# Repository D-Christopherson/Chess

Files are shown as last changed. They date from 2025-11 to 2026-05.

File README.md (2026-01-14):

This repo contains all the relevant files for a chess board I'm building.

The top level directory contains a chess engine I wrote in Kotlin, serve with Spring Boot, and deploy to AWS with Terraform.
I'd written a chess engine in Java using two-dimensional arrays to represent the board early on in college, so I wanted 
to try bitboards this time. The goal is to represent the board as a set of 64-bit numbers since operations with those should 
be much faster than an array. 

Some hand wavy math for moving a rook up one square:
* One clock cycle to multiply the first index by the width of the outer array
* One clock cycle to add that to the base address of the array
* One clock cycle to multiply the second index by the data type the inner array contains
* One clock cycle to add that to the address calculated in step 2
* One clock cycle to null out that square
* Repeat above for the target square

With bitboards (ideally)
* One clock cycle to left shift the number representing the rook by 8

`chess_electronics` contains the schematic and PCB design for the circuit board that connects the microcontroller, RFID 
reader, and antennas together. These were created in KiCad.

`microcontroller` contains the code running on the ESP32. The microcontroller is responsible for controlling the 8 separate
8 way switches, driving the RFID reader over UART, and converting the RFID tags into pieces to create the actual game state.

`mobile_app` contains a proof of concept android app that reads the board state from the microcontroller over bluetooth 
and sends that state to the chess engine in AWS over the internet. The ESP32 could do this itself since it has Wi-Fi capabilities,
but it'd be a huge pain to reprogram the Wi-Fi credentials if I want to take the board to a club.

Here's an MS Paint breakdown of the board itself.

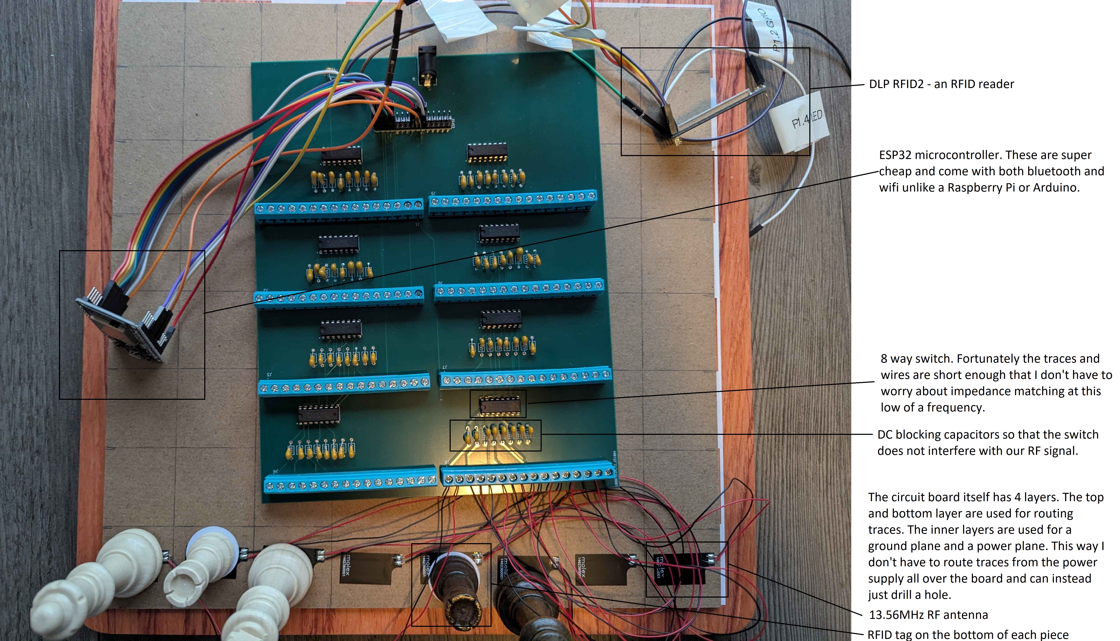
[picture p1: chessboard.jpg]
Chessboard


Eventually I'd like to strap an electromagnet to a pair of linear slides under the board to have the board play against 
a human. This product already exists, but costs between \$500 and \$1100.
The bill of materials for this build so far is:
* ESP32 dev board - $16 for a 3 pack on Amazon
* 8x SN74LV4051AN 8 way switch - $5.52 for 10 on DigiKey (cheaper than buying 8)
* 64x 13.56MHz RF antennas - $32 on DigiKey
* 65x 10nF ceramic capacitor - I bought a variety pack and used 47 nF capacitors after running out of 10nF. These will cost 
\$5-$30 on DigiKey. They just need to be capacitors that don't have polarity and are large enough to not add a ton of impedance 
(10nF is plenty).
* 8x 16 position screw terminals - $16 on DigiKey. I bought these not realizing that they're just 2 and 3 position terminals
connected to each other with a little plastic slide. Buying 64x 2 position terminals might be cheaper.
* DLP RFID2 - $37.95 on DigiKey. I've read that this chip is pretty outdated and has some firmware bugs. There might be 
something cheaper nowadays. The key is just to make sure it's compatible with the same frequency as the tags/antennas used 
and also has a pin for an external antenna.
* 5x circuit boards (as that's the minimum quantity most factories will make) - ~\$120. I also have a directory in `chess_electronics` 
called `Modular_Antenna` which crams the screw terminals and capacitors into a small board independent of one that would 
house the microcontroller and RFID reader (I have not designed this motherboard yet). This should bring the cost down to 
$30 or so since there's less wasted space. I'm just not sure if it's acceptable to run signal lines so close to other traces.

For the LCD screen you'll also need:
* 1x LCD screen - I'm using an LCD1602 module. It looks like these run \$5-\$10 depending on the source.
* 8x normally closed (Form B) relays. I quickly ran out of GPIO pins wiring each INH pin of the multiplexers to the
microcontroller directly, so these are going to connect the power plane to the INH pin. I'll have a 9th multiplexer that
connects to each of the relays. This brings the pins used for the multiplexers down to 6 from 11.
* 2x additional multiplexers. One for the multiplexer that now controls the INH pins and one for the LCD screen module.
The LCD screen has 8 data pins which the multiplexer will control as well as three pins for controlling the data on screen
and one pin for contrast.

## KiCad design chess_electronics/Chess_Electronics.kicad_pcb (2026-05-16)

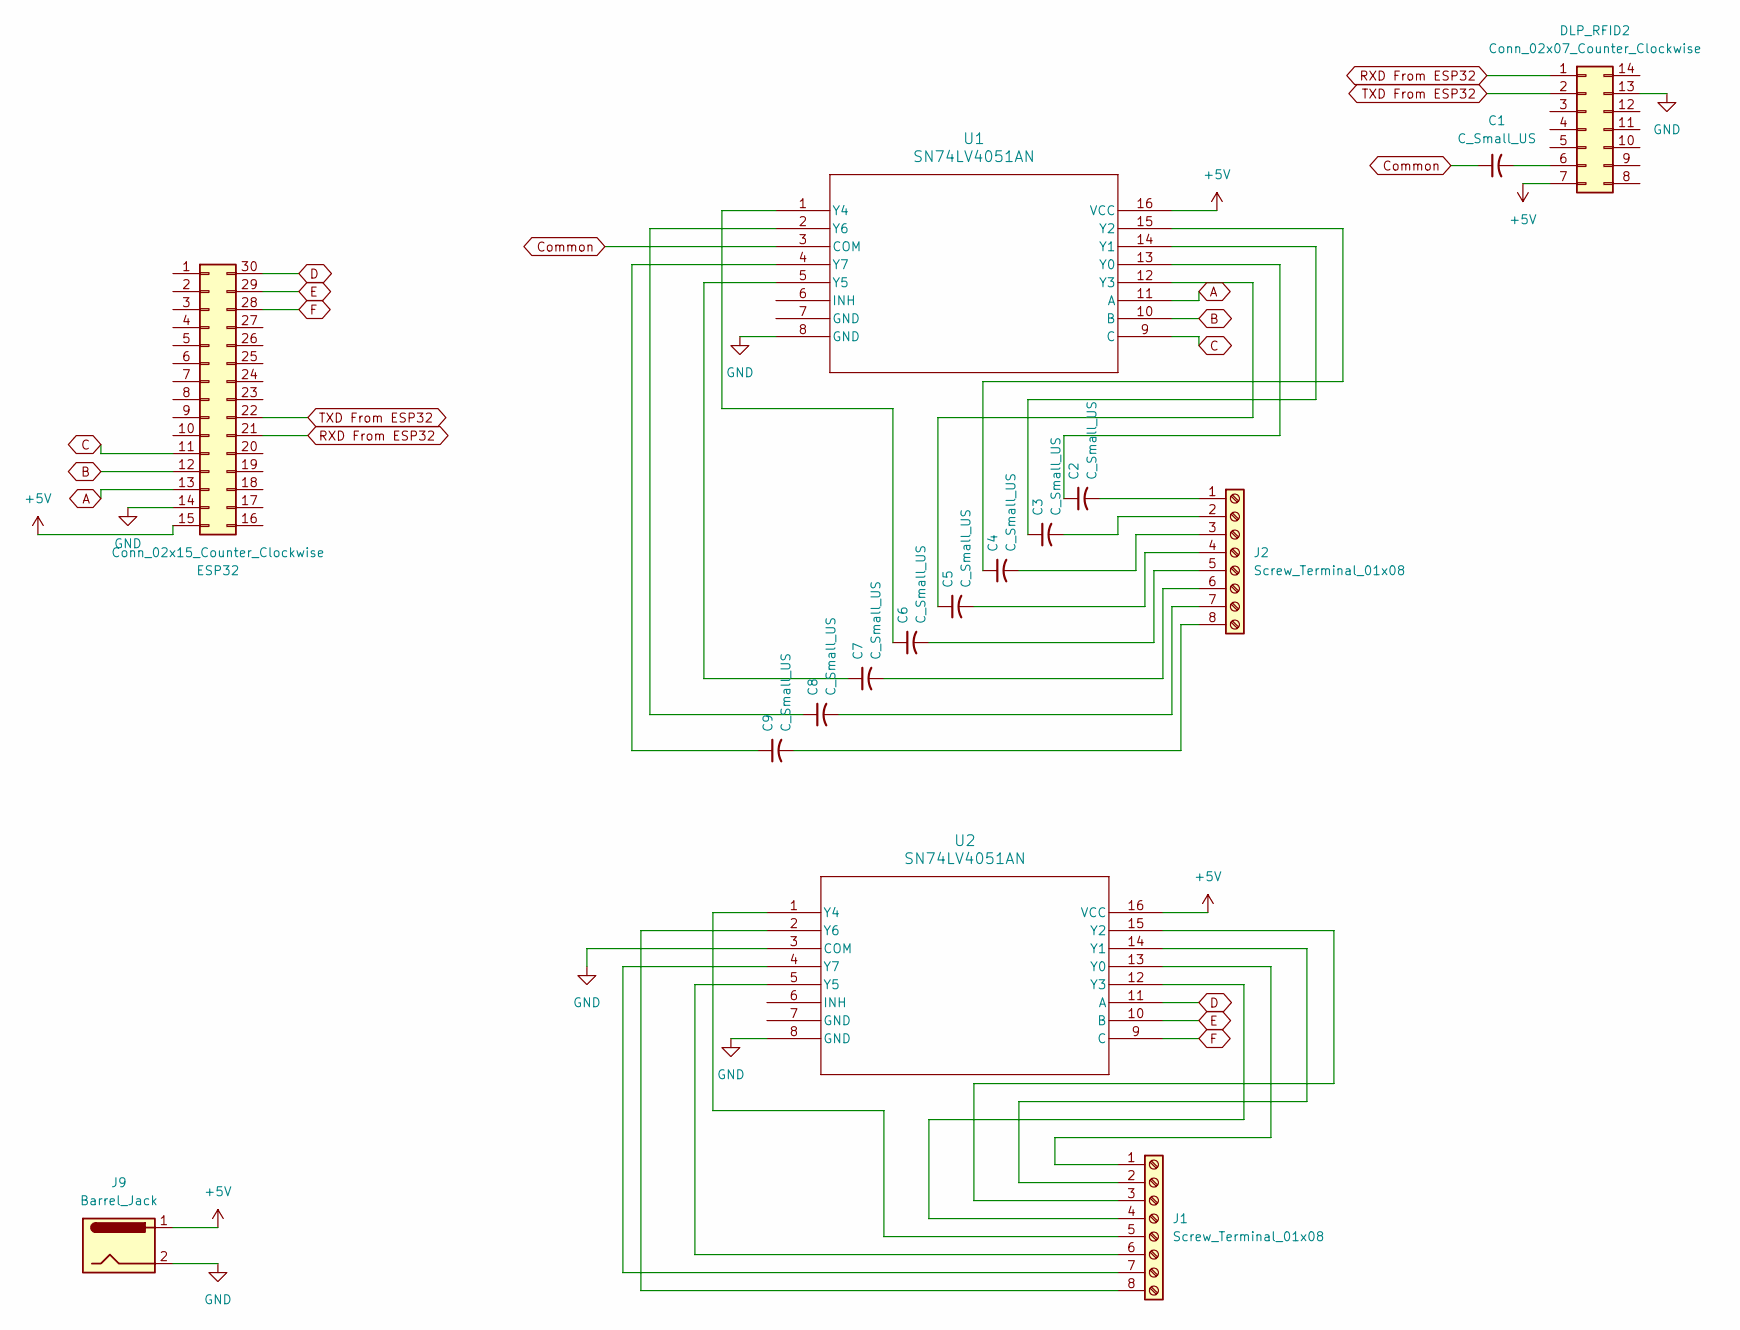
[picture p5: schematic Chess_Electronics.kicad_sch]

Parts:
C1, C2, C3, C4, C5, C6, C7, C8, C9: C_Small_US; C_Axial_L3.8mm_D2.6mm_P7.50mm_Horizontal
DLP_RFID2: Conn_02x07_Counter_Clockwise; PinHeader_2x07_P2.54mm_Vertical
ESP32: Conn_02x15_Counter_Clockwise; PinHeader_2x15_P2.54mm_Vertical
J1, J2: Screw_Terminal_01x08; TerminalBlock_MaiXu_MX126-5.0-08P_1x08_P5.00mm
J9: Barrel_Jack; CUI_PJ-037A
U1, U2: SN74LV4051AN; N16

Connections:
+5V: DLP_RFID2.7, ESP32.15, J9.1, U1.16 (VCC), U2.16 (VCC)
A: ESP32.13, U1.11 (A)
B: ESP32.12, U1.10 (B)
C: ESP32.11, U1.9 (C)
Common: C1.1, U1.3 (COM)
D: ESP32.30, U2.11 (A)
E: ESP32.29, U2.10 (B)
F: ESP32.28, U2.9 (C)
GND: DLP_RFID2.13, ESP32.14, J9.2, U1.8 (GND), U2.3 (COM), U2.8 (GND)
unnamed: C1.2, DLP_RFID2.6
unnamed: J1.1, U2.13 (Y0)
unnamed: J1.2, U2.14 (Y1)
unnamed: J1.3, U2.15 (Y2)
unnamed: J1.4, U2.12 (Y3)
unnamed: J1.5, U2.1 (Y4)
unnamed: J1.6, U2.5 (Y5)
unnamed: J1.7, U2.4 (Y7)
unnamed: J1.8, U2.2 (Y6)
unnamed: C2.2, J2.1
unnamed: C3.2, J2.2
unnamed: C4.2, J2.3
unnamed: C5.2, J2.4
unnamed: C6.2, J2.5
unnamed: C7.2, J2.6
unnamed: C8.2, J2.7
unnamed: C9.2, J2.8
unnamed: C2.1, U1.13 (Y0)
unnamed: C3.1, U1.14 (Y1)
unnamed: C4.1, U1.15 (Y2)
unnamed: C5.1, U1.12 (Y3)
unnamed: C6.1, U1.1 (Y4)
unnamed: C7.1, U1.5 (Y5)
unnamed: C8.1, U1.2 (Y6)
unnamed: C9.1, U1.4 (Y7)
RXD From ESP32: DLP_RFID2.1, ESP32.21
TXD From ESP32: DLP_RFID2.2, ESP32.22

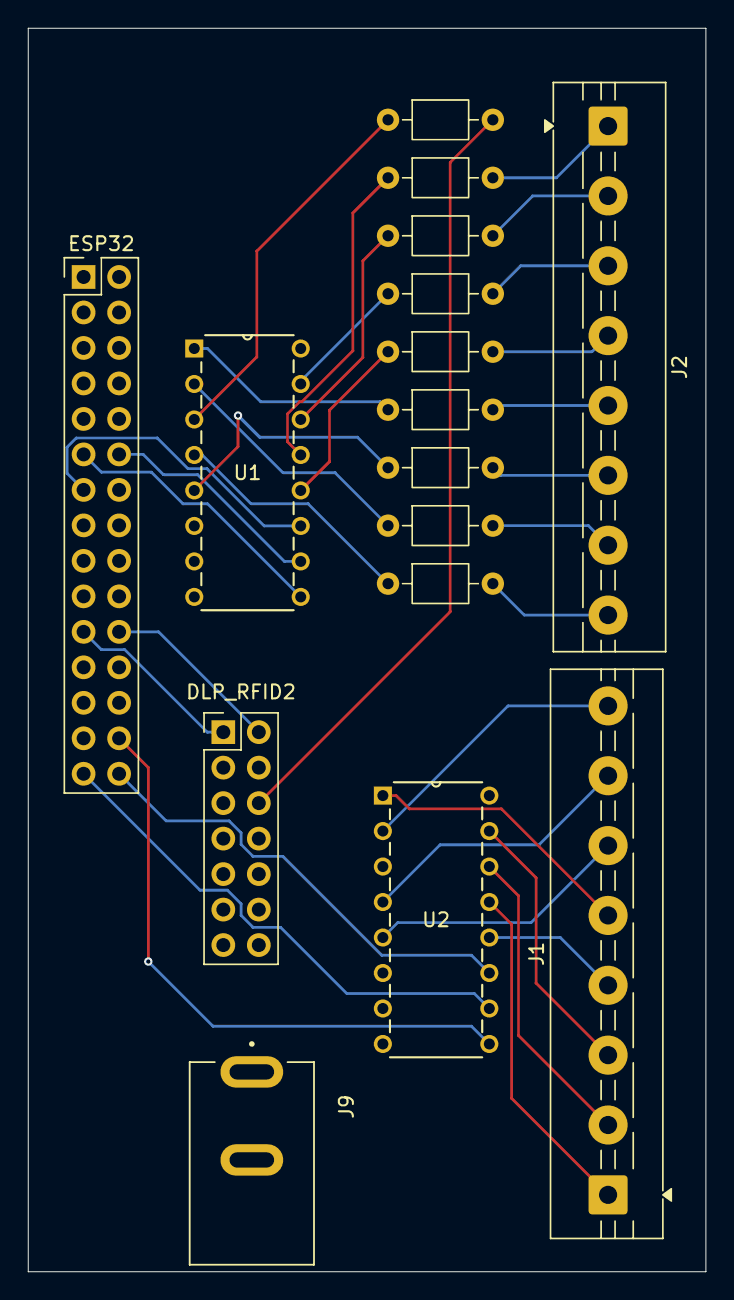
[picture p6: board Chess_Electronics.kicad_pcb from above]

Board: 4 copper layers, 48.5 x 89.0 mm, 16 parts (0 on the bottom side), 36 nets.

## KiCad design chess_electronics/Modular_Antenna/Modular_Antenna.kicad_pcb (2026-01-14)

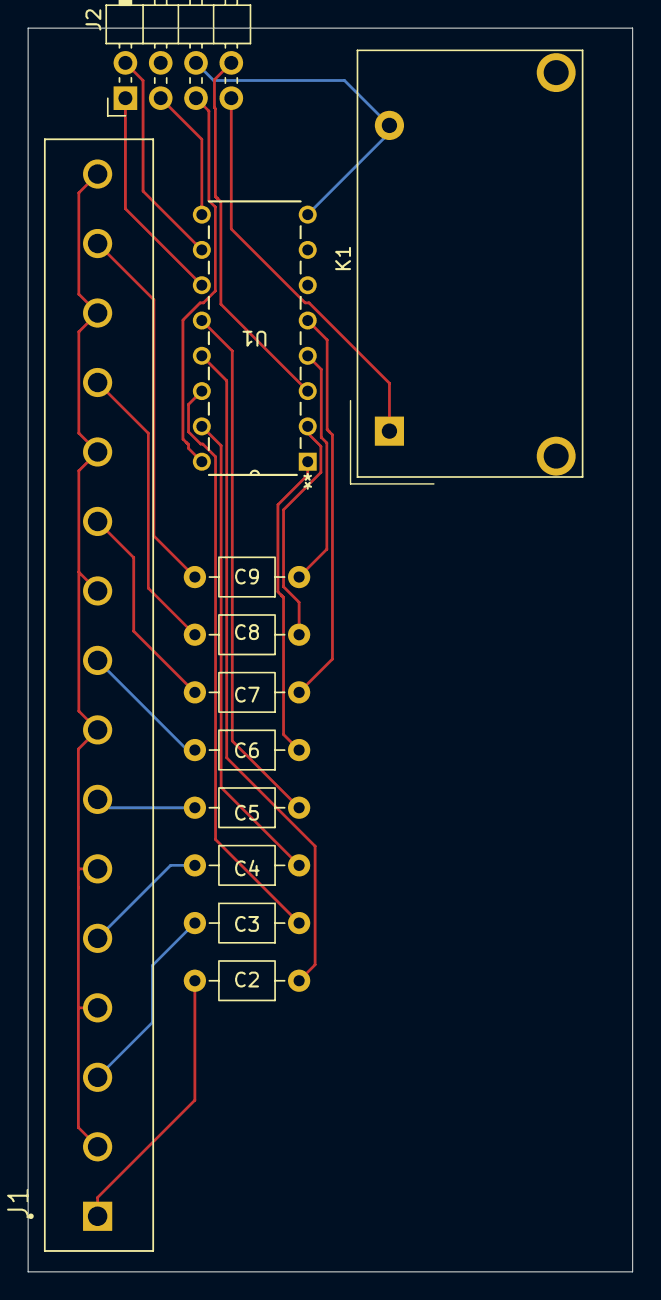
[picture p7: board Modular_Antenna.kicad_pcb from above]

Board: 2 copper layers, 43.5 x 89.5 mm, 12 parts (0 on the bottom side), 24 nets.

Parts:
C2, C3, C4, C5, C6, C7, C8, C9: C_Small_US; C_Axial_L3.8mm_D2.6mm_P7.50mm_Horizontal
J1: Screw_Terminal_01x16; CUI_TB003-500-P16BE
J2: Conn_02x04_Counter_Clockwise; PinHeader_2x04_P2.54mm_Horizontal
K1: Relay_SPST-NC; Relay_SPST_Zettler-AZSR131
U1: SN74LV4051AN; N16

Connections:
GND: J1.2, J1.4, J1.6, J1.8, J1.10, J1.12, J1.14, J1.16
unnamed: C2.2, J1.1
unnamed: C3.2, J1.3
unnamed: C4.2, J1.5
unnamed: C5.2, J1.7
unnamed: C6.2, J1.9
unnamed: C7.2, J1.11
unnamed: C8.2, J1.13
unnamed: C9.2, J1.15
unnamed: J2.1, U1.11 (A)
unnamed: J2.2, U1.10 (B)
unnamed: J2.3, U1.9 (C)
unnamed: J2.5, U1.16 (VCC)
unnamed: J2.6, K1.A2, U1.8 (GND)
unnamed: J2.7, K1.A1
unnamed: J2.8, U1.3 (COM)
unnamed: C2.1, U1.13 (Y0)
unnamed: C3.1, U1.14 (Y1)
unnamed: C4.1, U1.15 (Y2)
unnamed: C5.1, U1.12 (Y3)
unnamed: C6.1, U1.1 (Y4)
unnamed: C7.1, U1.5 (Y5)
unnamed: C8.1, U1.2 (Y6)
unnamed: C9.1, U1.4 (Y7)

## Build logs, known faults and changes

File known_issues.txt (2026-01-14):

Excessive object creation - I tried pooling Moves and the transposition entries so we could recycle them instead of instantiating
new objects as well as using Longs instead of ULongs (which are not primitives in Kotlin), but there was no meaningful
performance improvement.

No castling

No parameter to input previous board states to calculate 3-fold repetition

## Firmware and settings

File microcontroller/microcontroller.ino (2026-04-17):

#include <map>
#include <stdlib.h>
#include <string>
#include "BluetoothSerial.h"
#include "driver/uart.h"
#include "driver/gpio.h"
#include "freertos/FreeRTOS.h"
#include "freertos/task.h"
#include "freertos/queue.h"

// We're communicating with the RFID reader over UART. I've arbitrarily picked the second set of UART pins on my ESP32.
const int RXD_PIN = 16;
const int TXD_PIN = 17;
#define UART_NUM UART_NUM_2
static const int RX_BUF_SIZE = 4096;

// TODO this is not implemented yet. Sometimes the RFID reader gets into a wonky state and never returns meaningful information again.
// The reset pin can be used to return the reader into a good state without having to cycle power.
const int reset = 12;

// These will control the multiplexers wired to the rf antennas. The output of each will bbe wired together.
const int c1 = 21;
const int c2 = 19;
const int c3 = 18;


// The values to set the switch the multiplexer to each leg. 0,0,0 is y0, 0,0,1 is y1 etc. These are the values for the control pins above.
const int muxChannels[8][3] = {
  { 0, 0, 0 }, { 0, 0, 1 }, { 0, 1, 0 }, { 0, 1, 1 }, { 1, 0, 0 }, { 1, 0, 1 }, { 1, 1, 0 }, { 1, 1, 1 }
};

// The pins on the microcontroller that disable each switch. Even if the antennas aren't connected, the unused switches need to be disabled.
// I'm not sure what the cause is. Perhaps the screw terminals have too much capacitance. This ordering isn't particularly special, it's just 
// the order that the ESP32 dev board I have puts them in.
// INH pops up a lot in circuit diagrams and stands for "inhibit high" as in: supply the pin power and the switch shuts off.
const int muxInh[8] = {
  13, 12, 14, 27, 26, 25, 33, 32
};

QueueHandle_t uart_queue;

// The standard way to refer to pieces is one letter that is lowercase for black and uppercase for white.
// King - K, Queen - Q, Rook - R, Knight - N, Bishop - b, Pawn - p
// Unfortunately the reader seems to sometimes include extra characters or hallucinate additional tags, so I'll have to iterate through each key
// looking for something close.
// TODO - Need tags for additional queens, rooks, bishops, and pawns (both for promotion and the starting set of pieces)
const std::map<std::string, std::string> tagIdToPiece = {
  {"[04FA0D7B5A6F6180D4", "k"},
  {"[04711CE15A6F6180D4", "q"},
  {"[045E1BC95D6F6180D3", "r"},
  {"[047AAD596F6180", "b"},
  {"[04DD6A3B5D6F6180D3", "n"},
  {"[04F389F65A6F6180D4", "p"},

  {"[0440905C5A6F6180D4", "K"},
  {"[04EBE5825C6F6180D2", "Q"},
  {"[043E5DEF5D6F6180D3", "R"},
  {"[04BA0A606F6180", "B"},
  {"[04211AB75A6F6180D4", "N"},
  {"[047113606F6180", "P"}
};

// Wrangling 128 wires to the correct location on the circuit board seems a lot more difficult than just mapping it in software. 
// The first digit will be row, second will be column. To correct the mapping I'll set unique pieces on the first row and swap values with
// the correct square. Then move on to the second row and repeat.
// If I make a second revision of the circuit board, I'll silk screen the multiplexer values next to the screw terminals instead of this.
std::map<int, int> antennaLocationToSquare = {
  {00, 00}, {01, 01}, {02, 02}, {03, 03}, {04, 04}, {05, 05}, {06, 06}, {07, 07},
  {10, 10}, {11, 11}, {12, 12}, {13, 13}, {14, 14}, {15, 15}, {16, 16}, {17, 17},
  {20, 20}, {21, 21}, {22, 22}, {23, 23}, {24, 24}, {25, 25}, {26, 26}, {27, 27},
  {30, 30}, {31, 31}, {32, 32}, {33, 33}, {34, 34}, {35, 35}, {36, 36}, {37, 37},
  {40, 40}, {41, 41}, {42, 42}, {43, 43}, {44, 44}, {45, 45}, {46, 46}, {47, 47},
  {50, 50}, {51, 51}, {52, 52}, {53, 53}, {54, 54}, {55, 55}, {56, 56}, {57, 57},
  {60, 67}, {61, 66}, {62, 65}, {63, 64}, {64, 63}, {65, 62}, {66, 61}, {67, 60},
  {70, 70}, {71, 71}, {72, 72}, {73, 73}, {74, 74}, {75, 75}, {76, 76}, {77, 77},
};

BluetoothSerial SerialBT;

// TODO on interrupt reset queue or reader
// This is modified from Espressif's uart event example https://github.com/espressif/esp-idf/blob/v5.5.1/examples/peripherals/uart/uart_events/main/uart_events_example_main.c
// I've only seen these errors pop up when there's something wrong with my circuit and the reader gets into a bad state, but I'm leaving it in
// for visibility in case it happens again in the future.
static void uart_event_task(void* pvParameters) {
  uart_event_t event;
  size_t buffered_size;
  uint8_t* dtmp = (uint8_t*)malloc(1024);
  for (;;) {
    if (xQueueReceive(uart_queue, (void*)&event, (TickType_t)portMAX_DELAY)) {
      bzero(dtmp, 1024);
      switch (event.type) {
        case UART_DATA:
          break;
        case UART_FIFO_OVF:
          //Serial.println("hw fifo overflow");
          uart_flush_input(UART_NUM);
          xQueueReset(uart_queue);
          break;
        case UART_BUFFER_FULL:
          //Serial.println("ring buffer full");
          uart_flush_input(UART_NUM);
          xQueueReset(uart_queue);
          break;
        case UART_BREAK:
          //Serial.println("uart rx break");
          break;
        case UART_PARITY_ERR:
          //Serial.println("uart parity error");
          break;
        case UART_FRAME_ERR:
          //Serial.println("uart frame error");
          break;
        case UART_PATTERN_DET:
          uart_get_buffered_data_len(UART_NUM, &buffered_size);
          //Serial.println("[UART PATTERN DETECTED] pos: %d, buffered size: %d");
          break;
        default:
          //Serial.println("Event type");
          //Serial.println(event.type);
          break;
      }
    }
  }
  free(dtmp);
  dtmp = NULL;
  vTaskDelete(NULL);
}


/**
* Sends a command over UART to the RFID reader. Output will be stored in the data buffer.
*/
void sendUartCommand(uint8_t* data, char* command) {
  // The commands for the RFID reader are written in hex as specified by the docs. But it doesn't want the values in hex,
  // it wants the ASCII representation of the hex. So I'll be printing the commands to a string and sending that.
  int len = sprintf((char*)data, command);
  uart_write_bytes(UART_NUM, data, len);
  delay(1);

  int rxBytes = uart_read_bytes(UART_NUM, data, RX_BUF_SIZE, 200 / portTICK_PERIOD_MS);
  if (rxBytes > 0) {
    data[rxBytes] = 0;
    //Serial.print((char*)data);

  } else {
    //Serial.println("No data");
  }
  delay(1);
}

void setup() {
  Serial.begin(115200);
  Serial.println("Booting");

  SerialBT.begin("Chess");  // Bluetooth device name

  // Set the switches to y0
  pinMode(c1, OUTPUT);
  pinMode(c2, OUTPUT);
  pinMode(c3, OUTPUT);
  digitalWrite(c1, LOW);
  digitalWrite(c2, LOW);
  digitalWrite(c3, LOW);

  // Turn all of our switches off
  for (int inhPin : muxInh) {
    pinMode(inhPin, OUTPUT);
    digitalWrite(inhPin, HIGH);
  }

  // UART configuration lifted almost verbatim from https://controllerstech.com/how-to-use-uart-in-esp32-esp-idf/
  const uart_config_t uart_config = {
    .baud_rate = 115200,
    .data_bits = UART_DATA_8_BITS,
    .parity = UART_PARITY_DISABLE,
    .stop_bits = UART_STOP_BITS_1,
    .flow_ctrl = UART_HW_FLOWCTRL_DISABLE,
    .source_clk = UART_SCLK_DEFAULT,
  };


  int result = uart_driver_install(UART_NUM, RX_BUF_SIZE, 0, 10, &uart_queue, 0);
  if (result != ESP_OK) {
    // I'm not sure what I'd even want to do if this happens. Maybe restart the microcontroller? Luckily it hasn't popped up yet.
    //Serial.println("Failed to install UART driver");
  }

  xTaskCreate(uart_event_task, "uart_event_task", 3072, NULL, 12, NULL);

  uart_param_config(UART_NUM, &uart_config);
  ESP_ERROR_CHECK(uart_set_pin(UART_NUM, TXD_PIN, RXD_PIN, UART_PIN_NO_CHANGE, UART_PIN_NO_CHANGE));
  uint8_t* data = (uint8_t*)malloc(RX_BUF_SIZE * 2);
  int len = 0;
  delay(100);

  // I couldn't find out what this does in the docs. The GUI sends it, and it does seem to matter. The GUI can be found
  // here https://www.dlpdesign.com/rfrdr/ and it's a great tool to determine if there's something wrong with my circuit/commands
  // or the reader itself. I picked up a cheap USB to UART converter to test with.
  //Serial.println("Begin Setup");
  sendUartCommand(data, "010A0003041001210000");


  //Serial.println("Retrieving firmware version");
  sendUartCommand(data, "0108000304FE0000");

  // The DLP RFID2 comes with an internal antenna and a pin to connect an external antenna to. I'm using several switches to
  // multiplex to that one pin.
  //Serial.println("Enable external antenna");
  sendUartCommand(data, "01080003042B0000");

  // These three commands were what the GUI sent when selecting the ISO14443A protocol. The latter two seem to help correct
  // weak or slightly malformed signals.
  //Serial.println("ISO14443A setup");
  sendUartCommand(data, "010C00030410002101090000");
  //Serial.println("Sending AGC Toggle");
  sendUartCommand(data, "0109000304F0000000");
  //Serial.println("Sending AM PM Toggle");
  sendUartCommand(data, "0109000304F1FF0000");

  free(data);
}

void loop() {
  uint8_t* data = (uint8_t*)malloc(RX_BUF_SIZE * 2);
  if (SerialBT.isReady()) {
    String command = SerialBT.readStringUntil('#');
    Serial.println(command);
    if (command.compareTo("SCAN") == 0) {
      Serial.println("Scanning");
      // For now there's only one action. Later there might be instruction for the LCD screen or moving the stepper motors.
    } else {
      Serial.println("Unrecognized command");
      free(data);
      return;
     }
  } else {
    free(data);
    Serial.println("Unable to connect via bluetooth");
    return;
  }
  
  // This makes me miss Kotlin's initialization functions
  std::string board[8][8];
  for (int i = 0; i < 8; i++) {
    for (int j = 0; j < 8; j++) {
      board[i][j] = "-";
    }
  }

  iterateMuxes(data, board);

  std::string fen = "";
  int emptySquares = 0;
  // Retrieve board state and convert to FEN.
  // I haven't thought about how I'm going to track state like which turn it is or if there's an en-passant square. That might be better
  // to do in the mobile app with a toggle for whose move it is.
  for(int i = 0; i < 8; i++) {
    for (int j = 0; j < 8; j++) {
      Serial.print(board[i][j].c_str());
      if (board[i][j] != "-") {
        if (emptySquares > 0) {
          fen += std::to_string(emptySquares);
          emptySquares = 0;
        }
        fen += board[i][j];
      } else {
        emptySquares++;
      }
    }
    if (emptySquares > 0) {
      fen += std::to_string(emptySquares);
    }
    if (i != 7) {
      fen += "/";
    }
    emptySquares = 0;
    Serial.println();
  }

  // The state I'm not tracking yet. Side to move, castling rights, en-passant square, half move clock, full move clock
  fen += " w KQkq - 0 0";
  Serial.println(fen.c_str());

  free(data);
  SerialBT.write((uint8_t*)fen.c_str(), fen.length());
  Serial.println("Sent FEN over bluetooth");
  return;
}


void setMuxControlPins(int pin) {
  digitalWrite(c1, muxChannels[pin][0]);
  digitalWrite(c2, muxChannels[pin][1]);
  digitalWrite(c3, muxChannels[pin][2]);
  delay(1);
}

void setInhPins(int lowPin) {
  for (int inhPin : muxInh) {
    (inhPin == lowPin) ? digitalWrite(inhPin, LOW) : digitalWrite(inhPin, HIGH);
  }
  delay(1);
}

void iterateMuxes(uint8_t* data, std::string board[8][8]) {
  int i = 0;
  for (int inhPin : muxInh) {
    setInhPins(inhPin);
    //Serial.println("Mux: " + String(inhPin));
    for (int j = 0; j < 8; j++) {
      //Serial.println("Mux pin: y" + String(j));

      // Swap antennas
      setMuxControlPins(j);


      //Serial.println("Inventory Tags");
      sendUartCommand(data, "0109000304A0010000");

      std::string tag((char*) data);
      for (auto tagToPiece : tagIdToPiece) {
        if (tag.find(tagToPiece.first) != std::string::npos) {
          //Serial.println(tagToPiece.second.c_str());
          int boardLocation = antennaLocationToSquare[i * 10 + j];
          board[boardLocation / 10][boardLocation % 10] = tagToPiece.second.c_str();
        }
      }

    }
    i++;
  }
}

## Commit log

2025-11-22 Add initial pass of microcontroller code. It currently scans all 64 antennas and reports the FEN to the mobile app over bluetooth
2025-11-22 Add proof of concept for mobile app. It breaks most design rules running everything on the main thread
2025-12-09 Add circuitboard schematic and pcb design
    [Chess_Electronics-B_Cu.gbr, Chess_Electronics-B_Mask.gbr, Chess_Electronics-B_Paste.gbr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]
2026-01-14 Add normally closed relay to modular antenna design
    [Modular_Antenna.kicad_pcb, Modular_Antenna.kicad_sch]
2026-01-14 Update evaluate API to additionally return evaluation and depth, add simple auth filter
2026-04-13 Add inital UI design for board and pieces
2026-04-13 Switch to jetpack compose instead of using a layout
2026-04-17 Reverse direction of control so the mobile app drives the microcontroller and add buttons for scanning/eval
    [microcontroller.ino]
2026-04-29 Switch from explicit threads to coroutines. Also move button implementation into each composable by using a function to write state back to the parent
2026-05-16 Update PCB to use two multiplexers by chaining signal and ground in opposite directions
    [Chess_Electronics.kicad_pcb, Chess_Electronics.kicad_sch]
2026-06-24 Add API to route pieces on the gantry. Also upgrade to Spring Boot 4
